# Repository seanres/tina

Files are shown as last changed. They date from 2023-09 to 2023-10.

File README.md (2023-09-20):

# tira
Robot arm project for UConn's robotics club!

WIP page

## To Do:

- [ ] Order materials

Mechanical
- [ ] Design review
- [ ] 3D printing process
- [ ] Print arm components
- [ ] Overall solidoworks part design
- [ ] Assembly in solidworks
- [ ] Modifying design for gears
- [ ] Blueprints?
- [ ] Machining process
- [ ] Machining aluminum parts

Electrical
- [ ] Electrical design review
- [ ] Review basic electronics (laser video)
- [ ] Soldering/wiring overview
- [ ] Review microcontrollers/arduinos
- [ ] Basic motor control 
- [ ] Assemble circuitry

Digital
- [ ] Programming for arudino
- [ ] ROS introduction
- [ ] ROS for robot arm
- [ ] More advanced ROS control
- [ ] Control theory? (PID)
- [ ] Communication? (I2C, serial)

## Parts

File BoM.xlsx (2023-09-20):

Notes | Name | Link | # Reqd. | # per Unit | Unit Cost | # To Order | Total
 | Motors:
 | Nema 8 (8HS13-0604S) 33mm | https://www.oyostepper.com/goods-3-Nema-8-Stepper-Motor-Bipolar-18-deg-2Ncm-283ozin-06A-39V-20x20x33mm-4-Wires.html | 1 | 1 | $22.36 | 1 | $22.36
 | Nema 11 (11HS12-0674S) 31mm | https://www.omc-stepperonline.com/nema-11-bipolar-1-8deg-7ncm-9-91oz-in-0-67a-3-8v-28x28x31mm-4-wires-11hs12-0674s | 2 | 1 | $10.18 | 2 | $20.36
 | Nema 17 (17HS19-0854S) 48mm | https://www.omc-stepperonline.com/nema-17-bipolar-1-8deg-44ncm-62-3oz-in-0-85a-5-3v-42x42x48mm-4-wires-17hs19-0854s | 1 | 1 | $10.85 | 1 | $10.85
 | Nema 23 (23HS30-2804S1) 76mm | https://www.omc-stepperonline.com/nema-23-bipolar-1-9nm-269oz-in-2-8a-57x57x76mm-4wires-6mm-shaft-23hs30-2804s1 | 2 | 1 | $29.85 | 2 | $59.70
https://shop.sdp-si.com/catalog/?cid=p342&sort=undefined&view=table | Belts: |  |  |  |  |  | $0.00
 | A 6R51M087060, 87 teeth GT2 2mm, 6mm wide timing belt | https://shop.sdp-si.com/catalog/product/?id=A_6R51M087060 | 2 | 1 | $6.71 | 2 | $13.42
 | A 6R51M139060, 139 teeth GT2 2mm, 6mm wide timing belt | https://shop.sdp-si.com/catalog/product/?id=A_6R51M139060 | 1 | 1 | $7.67 | 1 | $7.67
OOS, 2mm pitch instead | A 6R53M128090, 128 teeth GT2 3mm, 9mm wide timing belt | https://shop.sdp-si.com/catalog/product/?id=A_6R51M128090 | 1 | 1 | $10.14 | 1 | $10.14
OOS, 2mm pitch instead | A 6R53M152090, 152 teeth GT2 3mm, 9mm wide timing belt | https://shop.sdp-si.com/catalog/product/?id=A36R51M152090 | 1 | 1 | $8.09 | 1 | $8.09
https://shop.sdp-si.com/catalog/?cid=p346 | Pulleys: |  |  |  |  |  | $0.00
 | GT2 Pulley (20 Tooth), GT2 2mm, 20 teeth, 5mm bore | https://quantum3dprinting.com/shop/genuine-e3d-2gt-pulley-20-tooth-m-2gt-pulley-20t/ | 3 | 1 | $10.98 | 3 | $32.94
 | A 6A53M020DF0906, GT2 3mm, 20 teeth, 6mm bore | https://shop.sdp-si.com/catalog/product/?id=A_6A53M020DF0906 | 2 | 1 | $10.88 | 2 | $21.76
 | Bearings: |  |  |  |  |  | $0.00
DISCONTINUED, NEED ALTERNATIVE | Ball Bearing, 21x15x4mm |  | 3 | 4 | $8.59 | 1 | $8.59
 | Ball Bearing, 16x8x5mm | https://www.amazon.com/Hobbypower-8x16x5mm-Shielded-16x8x5mm-Bearings/dp/B07WVJWQZS | 3 | 10 | $7.99 | 1 | $7.99
DISCONTINUED, NEED ALTERNATIVE | Ball Bearing, 8x3x3mm |  | 4 | 1 | $2.00 | 4 | $8.00
 | Q6000 ZZ, 26x10x8mm | https://www.amazon.com/FKG-6000-ZZ-10x26x8mm-Bearing-Pre-Lubricated/dp/B07T59CWXX | 2 | 19 | $9.97 | 1 | $9.97
 | Q625 ZZ, 16x5x5mm | https://www.ebay.com/itm/333771184305 | 4 | 6 | $7.68 | 1 | $7.68
 | Q6001 ZZ, 28x12x8mm | https://www.amazon.com/PGN-6001-ZZ-Shielded-Ball-Bearing/dp/B07GVQ6K9R?s=industrial | 2 | 10 | $10.90 | 1 | $10.90
European, need to find US source | TB51102, 28x16x28x15x9mm | https://www.amazon.com/51102-Thrust-Bearing-15x28x9-Bearings/dp/B002BBKMZO | 2 | 1 | $10.00 | 2 | $20.00
 | Carbon Fiber:
 | Axis3part1 (3mm thickness) |  | 2 |  |  |  | $200.00
 | Axis2part1 (4mm thickness) |  | 2
 | Axis1part2 (4mm thickness) |  | 2
 | Screws and Nuts:
 | M2x6mm |  | 1
 | M2x8mm + nut |  | 4
 | M2x12mm + nut |  | 3
 | M2x10mm + nut |  | 1
 | M2.5x8mm + washer |  | 8
 | M3x10mm + nut + washer |  | 1
 | M3x12mm + nut + washer |  | 14
 | M3x16mm + nut + washer |  | 2
 | M3x20mm + nut + washer |  | 6
 | M3x25mm + washer |  | 4
 | M3x25mm + nut |  | 1
 | M3x30mm + nut + washer |  | 6
 | M3 washer |  | 10
 | M4x12mm + nut + washer |  | 8
 | M5x10mm + washer |  | 12
 | M5x20mm + washer |  | 2
 | M5x35mm + nut + washer |  | 4
 | M5x40mm + nut + washer |  | 1
 | M5x50mm + nut + washer |  | 16
 | M5 washer |  | 10
 | M5 threaded standoff, 8mm OD, 20mm Len |  | 7
 |  | https://www.amazon.com/VIGRUE-M2-M3-M4-1080PCS-Stainless-Screws-Socket/dp/B071KBVZVV?s=industrial | 1 |  | estimate: | 2 | 50
 | Other Parts:
 | Magnet 6mm diameter, 2mm height
 | DP2.0-6/B, dowel pin 2x6
 | Tube: 8mm OD, 6mm, ID, 70mm Len
 | Tube: 10mm OD, 8mm ID, 115m len
 | Tube: 12mm OD, 10mm ID, 106mm len
 | Silicon insulated high quality wires
 | Rubber feed with M3 set
 |  |  |  |  |  |  | 60
 | Controllers:
KIT #1 | A4988 Stepper Motor Driver Module | https://www.amazon.com/Stepper-Printer-StepStick-Envistia-Mall/dp/B07QT7N3T2 | 3 | 2 | $5.89 | 0
 | TB6600 4A 9-42V stepper motor driver | https://www.amazon.com/TB6600-Stepper-Driver-Controller-tb6600/dp/B07RRB6BGQ | 3 | 4 | $33.99 | 1
 | Microcontroller:
KIT #1 | 3D printer RAMPS control board | https://www.amazon.com/Controller-MEGA2560-Soldered-Stepper-Drivers/dp/B08N578PRN | 1 | 1 | $31.39 | 1
KIT #1 | Arduino Mega 2560 |  | 1
 | Connectors:
 | D-sub 25, male connector |  | 1 |  |  |  | 5
 | D-sub 25, female connector |  | 1 |  |  |  | 5
 | Wires:
 | D-sub 25 male - D-sub 25 female, 3.0Amp rating |  | 1 |  |  |  | 10
 | Miscillaneous:
 | Soddering Iron Kit | https://www.amazon.com/gp/product/B00ANZRT4M/ref=ppx_yo_dt_b_search_asin_title?ie=UTF8&psc=1 | 1 |  | $75.99 |  | 115
 | Soddering Iron Wire Holder |  | 1
 |  |  |  |  |  | SUM: | $725.42

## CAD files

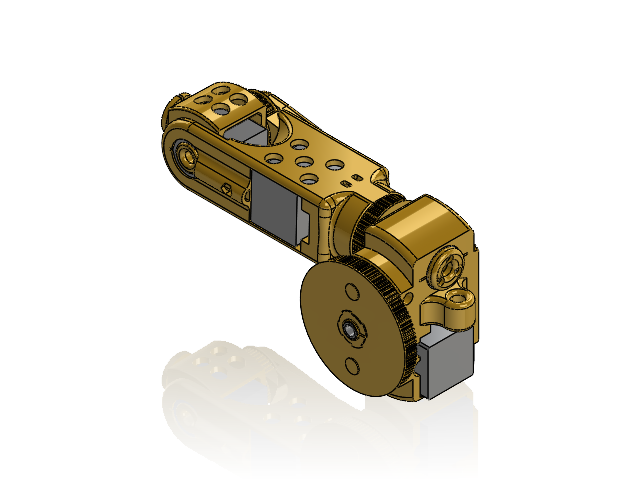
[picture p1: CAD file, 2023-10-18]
SolidWorks/upper_assembly.SLDASM
Bearing21_15_4_3 x 3
Pulley42
Bearing16_8_5_1_1
Nema8_1
Axis6_1
axis6motorHolder_1
Pulley100
Pulley56
Nema11_2 x 2
Axis5
Axis4
Axis5Bracket
Axis4limit
Axis5plug
Axis5screwHolder
Axis3tube

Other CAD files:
SolidWorks/Bearing16_8_5_3.SLDASM
SolidWorks/Bearing16_8_5.SLDASM
SolidWorks/Axis2part1_1.SLDASM
SolidWorks/Bearing26_10_8.SLDASM
SolidWorks/Axis3part1_1.SLDASM
SolidWorks/Nema11.SLDASM
SolidWorks/Axis5Pulley.SLDASM
SolidWorks/Axis1Pulley.SLDASM
SolidWorks/Bearing28_12_8_1.SLDASM
SolidWorks/Bearing21_15_4.SLDASM
SolidWorks/Nema17.SLDASM
SolidWorks/Axis3part1.SLDASM
SolidWorks/Axis1part2.SLDASM
SolidWorks/Axis6.SLDASM
SolidWorks/Axis3Pulley.SLDASM
SolidWorks/axis6motorHolder.SLDASM
SolidWorks/ThrustBearing28_15_9_1.SLDASM
Axis/Axis1tube.f3d
Axis/Axis1tube.step
Axis/Axis2tube.f3d
Axis/Axis2tube.step
Axis/Axis3tube.f3d
Axis/Axis3tube.step
CarbonFibre/Axis1part2.DXF
CarbonFibre/Axis1part2.stl
CarbonFibre/Axis2part1.DXF
CarbonFibre/Axis2part1.stl
CarbonFibre/Axis3part1.DXF
CarbonFibre/Axis3part1.stl
Fusion360/Axis6 v13.step
Fusion360/AxisTot1 v14.step
Fusion360/AxisTot1.f3z
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

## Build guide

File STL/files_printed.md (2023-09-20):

Axis1Holder.stl - x1 unit
Axis1MotorHolder.stl - x1 unit
Axis1MotorHolderOp.stl - x1 unit
Axis1part2.stl - x2 units (optional, only if you do not have carbon fibre parts)
Axis1Pulley.stl - x1 unit
Axis1washer.stl - x1 unit
Axis2bearingHC.stl - x1 unit
Axis2bearingHolder (1).stl - x1 unit
Axis2bearingHolder.stl - x1 unit
Axis2MotorOp.stl - x1 unit
Axis2MotorOpC.stl - x1 unit
Axis2part1.stl - x2 units (optional, only if you do not have carbon fibre parts)
Axis2part2.stl - x1 unit
Axis2Pulley.stl - x1 unit
Axis2washer.stl - x1 unit
Axis3bearingHolder.stl - x2 units
Axis3cover1.stl - x1 unit
Axis3cover2.stl - x1 unit
Axis3part1.stl - x2 units (optional, only if you do not have carbon fibre parts)
Axis3part2.stl - x1 unit
Axis3part3.stl - x1 unit
Axis4.stl - x1 unit
Axis4limit.stl - x1 unit
- [X] Axis5.stl - x1 unit
- [X] Axis5Bracket.stl - x1 unit
- [X] Axis5plug.stl - x1 unit
- [X] Axis5screwHolder.stl - x1 unit
- [X] Axis6.stl - x1 unit
- [X] axis6motorHolder.stl - x1 unit
FootHolder.stl - x2 units
LegLeft.stl - x1 unit and x1 unit mirrored part
Pulley42.stl - x1 unit
Pulley56.stl - x1 unit
Pulley100.stl - x1 unit
Electronics.stl - support for the Arduino and TB6600 drivers for electronics

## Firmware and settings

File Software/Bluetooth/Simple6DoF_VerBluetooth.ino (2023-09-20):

/*
Simple script to move my tiny 6dof robotic arm
*/
#include <math.h>
//#include <SoftwareSerial.h>

#define PI 3.1415926535897932384626433832795

//driver for the axis 1
#define PUL1_PIN 39
#define DIR1_PIN 37
//driver for the axis 2
#define PUL2_PIN 43
#define DIR2_PIN 41
//driver for the axis 3
#define PUL3_PIN 47
#define DIR3_PIN 45
//driver for the axis 4
#define PUL4_PIN 46
#define DIR4_PIN 48
//driver for the axis 5
#define PUL5_PIN A6
#define DIR5_PIN A7
//driver for the axis 6
#define PUL6_PIN A0
#define DIR6_PIN A1

//enable pin for the axis 3, 2 and 1
#define EN321_PIN 32
#define EN4_PIN A8
#define EN5_PIN A2
#define EN6_PIN 38

double curPos1 = 0.0;
double curPos2 = -78.51;
double curPos3 = 73.90;
double curPos4 = 0.0;
double curPos5 = -90.0;
double curPos6 = 0.0;

boolean PULstat1 = 0;
boolean PULstat2 = 0;
boolean PULstat3 = 0;
boolean PULstat4 = 0;
boolean PULstat5 = 0;
boolean PULstat6 = 0;

//robot geometry
const double dl1 = 360.0/200.0/32.0/4.8;
const double dl2 = 360.0/200.0/32.0/4.0;
const double dl3 = 360.0/200.0/32.0/5.0;
const double dl4 = 360.0/200.0/32.0/2.8;
const double dl5 = 360.0/200.0/32.0/2.1;
const double dl6 = 360.0/200.0/32.0/1.0;
const double r1 = 47.0;
const double r2 = 110.0;
const double r3 = 26.0; 
const double d1 = 133.0;
const double d3 = 0.0;
const double d4 = 117.50;
const double d6 = 28.0;

//SoftwareSerial Bluetooth(29, 31); // Arduino(RX, TX) - HC-05 Bluetooth (TX, RX)
String dataIn = ""; //variable to store the bluetooth command
double futPos1 = 0.0;
double futPos2 = 0.0;
double futPos3 = 0.0;
double futPos4 = 0.0;
double futPos5 = 0.0;
double futPos6 = 0.0;
double curSpeed = 0.3*0.5e-4;
double curFinalSpeed = 0.0;
int index = 0; //index corresonding to the robot position
float Joint1[50], Joint2[50], Joint3[50], Joint4[50], Joint5[50], Joint6[50], MaxSpeed[50], InSpeed[50], FinSpeed[50];

void setup()
{
  //Bluetooth.begin(38400); // Default baud rate of the Bluetooth module
  //Bluetooth.setTimeout(1);
  Serial1.begin(9600);
  //Serial1.setTimeout(3);
  delay(20);

  pinMode(PUL1_PIN, OUTPUT);
  pinMode(DIR1_PIN, OUTPUT);
  pinMode(PUL2_PIN, OUTPUT);
  pinMode(DIR2_PIN, OUTPUT);
  pinMode(PUL3_PIN, OUTPUT);
  pinMode(DIR3_PIN, OUTPUT);
  pinMode(PUL4_PIN, OUTPUT);
  pinMode(DIR4_PIN, OUTPUT);
  pinMode(PUL5_PIN, OUTPUT);
  pinMode(DIR5_PIN, OUTPUT);
  pinMode(PUL6_PIN, OUTPUT);
  pinMode(DIR6_PIN, OUTPUT);

  pinMode(EN321_PIN, OUTPUT);
  pinMode(EN4_PIN, OUTPUT);
  pinMode(EN5_PIN, OUTPUT);
  pinMode(EN6_PIN, OUTPUT);
  
  digitalWrite(PUL1_PIN, LOW); // gear ratio = 96/20 = 4.8
  digitalWrite(DIR1_PIN, LOW); //LOW = negative direction
  
  digitalWrite(PUL2_PIN, LOW); // gear ratio = 4
  digitalWrite(DIR2_PIN, LOW); //LOW = positive direction
  
  digitalWrite(PUL3_PIN, LOW); // gear ratio = 5
  digitalWrite(DIR3_PIN, LOW); //LOW = negative direction
  
  digitalWrite(PUL4_PIN, LOW); // gear ratio = 56/20 = 2.8
  digitalWrite(DIR4_PIN, LOW); //LOW = positive direction
  
  digitalWrite(PUL5_PIN, LOW); // gear ratio = 42/20 = 2.1
  digitalWrite(DIR5_PIN, LOW); //LOW = positive direction
  
  digitalWrite(PUL6_PIN, LOW); // gear ratio = 1
  digitalWrite(DIR6_PIN, LOW); //LOW = positive direction

  // all joints disabled!
  digitalWrite(EN321_PIN, HIGH);
  digitalWrite(EN4_PIN, HIGH);
  digitalWrite(EN5_PIN, HIGH);
  digitalWrite(EN6_PIN, HIGH); 

  //Serial.begin(9600);
}

void loop()
{
  //Serial1.write("Hello");
  // Check for incoming data
  if (Serial1.available() > 0) {
    dataIn = Serial1.readString();  // Read the data as string

    //Serial.println(dataIn);
    if (dataIn == "enable") {
      digitalWrite(EN321_PIN, LOW);
      digitalWrite(EN4_PIN, LOW);
      digitalWrite(EN5_PIN, LOW);
      digitalWrite(EN6_PIN, LOW);
    }
    
    if (dataIn == "disable") {
      digitalWrite(EN321_PIN, HIGH);
      digitalWrite(EN4_PIN, HIGH);
      digitalWrite(EN5_PIN, HIGH);
      digitalWrite(EN6_PIN, HIGH);
    }

    if (dataIn.startsWith("s6")) {
      String dataInS = dataIn.substring(2, dataIn.length());
      futPos6 = dataInS.toFloat();
      float Jinitial[6]={curPos1, curPos2, curPos3, curPos4, curPos5, curPos6};
      float Jfinal[6]={curPos1, curPos2, curPos3, curPos4, curPos5, futPos6};
      goStrightLine(Jinitial, Jfinal, curSpeed, 0.75e-10, 0.0, 0.0);
    }

    if (dataIn.startsWith("s5")) {
      String dataInS = dataIn.substring(2, dataIn.length());
      futPos5 = dataInS.toFloat();
      float Jinitial[6]={curPos1, curPos2, curPos3, curPos4, curPos5, curPos6};
      float Jfinal[6]={curPos1, curPos2, curPos3, curPos4, futPos5, curPos6};
      goStrightLine(Jinitial, Jfinal, curSpeed, 0.75e-10, 0.0, 0.0);
    }

    if (dataIn.startsWith("s4")) {
      String dataInS = dataIn.substring(2, dataIn.length());
      futPos4 = dataInS.toFloat();
      float Jinitial[6]={curPos1, curPos2, curPos3, curPos4, curPos5, curPos6};
      float Jfinal[6]={curPos1, curPos2, curPos3, futPos4, curPos5, curPos6};
      goStrightLine(Jinitial, Jfinal, curSpeed, 0.75e-10, 0.0, 0.0);
    }

    if (dataIn.startsWith("s3")) {
      String dataInS = dataIn.substring(2, dataIn.length());
      futPos3 = dataInS.toFloat();
      float Jinitial[6]={curPos1, curPos2, curPos3, curPos4, curPos5, curPos6};
      float Jfinal[6]={curPos1, curPos2, futPos3, curPos4, curPos5, curPos6};
      goStrightLine(Jinitial, Jfinal, curSpeed, 0.75e-10, 0.0, 0.0);
    }

    if (dataIn.startsWith("s2")) {
      String dataInS = dataIn.substring(2, dataIn.length());
      futPos2 = dataInS.toFloat();
      float Jinitial[6]={curPos1, curPos2, curPos3, curPos4, curPos5, curPos6};
      float Jfinal[6]={curPos1, futPos2, curPos3, curPos4, curPos5, curPos6};
      goStrightLine(Jinitial, Jfinal, curSpeed, 0.75e-10, 0.0, 0.0);
    }
    
    if (dataIn.startsWith("s1")) {
      String dataInS = dataIn.substring(2, dataIn.length());
      futPos1 = dataInS.toFloat();
      float Jinitial[6]={curPos1, curPos2, curPos3, curPos4, curPos5, curPos6};
      float Jfinal[6]={futPos1, curPos2, curPos3, curPos4, curPos5, curPos6};
      goStrightLine(Jinitial, Jfinal, curSpeed, 0.75e-10, 0.0, 0.0);
    }

    // set the maximum speed for the move
    if (dataIn.startsWith("ss")) {
      String dataInS = dataIn.substring(2, dataIn.length());
      curSpeed = (dataInS.toFloat()/100)*0.5e-4;
    }

    // If button "SAVE" is pressed
    if (dataIn.startsWith("save")) {
      String dataInS = dataIn.substring(4, dataIn.length());
      InSpeed[index] = curFinalSpeed;
      curFinalSpeed = (dataInS.toFloat()/100)*0.5e-4;
      Joint1[index] = curPos1;  // save position into the array
      Joint2[index] = curPos2;
      Joint3[index] = curPos3;
      Joint4[index] = curPos4;
      Joint5[index] = curPos5;
      Joint6[index] = curPos6;
      MaxSpeed[index] = curSpeed;
      FinSpeed[index] = curFinalSpeed;
      index++;                        // Increase the array index
    }

    if ( dataIn == "reset") {
      index = 0;  // Index to 0
    }

    if (dataIn.startsWith("run")) {
      float Jinitial[6]={curPos1, curPos2, curPos3, curPos4, curPos5, curPos6};
      float Jfinal[6]={Joint1[0], Joint2[0], Joint3[0], Joint4[0], Joint5[0], Joint6[0]};
      goStrightLine(Jinitial, Jfinal, MaxSpeed[0], 0.75e-10, 0.0, 0.0);
      for (int i = 0; i <= index - 2; i++) {  // Run through all steps(index)
        float Jinitial[6]={Joint1[i], Joint2[i], Joint3[i], Joint4[i], Joint5[i], Joint6[i]};
        float Jfinal[6]={Joint1[i+1], Joint2[i+1], Joint3[i+1], Joint4[i+1], Joint5[i+1], Joint6[i+1]};
        goStrightLine(Jinitial, Jfinal, MaxSpeed[i+1], 0.75e-10, InSpeed[i+1], FinSpeed[i+1]);
      }
    }

  }
}


void goStrightLine(float* xfi, float* xff, float vel0, float acc0, float velini, float velfin){
  //
  float lmax = max(abs(xff[0]-xfi[0]),abs(xff[1]-xfi[1]));
  lmax = max(lmax,abs(xff[2]-xfi[2]));
  lmax = max(lmax,abs(xff[3]-xfi[3]));
  lmax = max(lmax,abs(xff[4]-xfi[4]));
  lmax = max(lmax,abs(xff[5]-xfi[5]));
  unsigned long preMil = micros();
  double l = 0.0;
  vel0 = min(vel0,sqrt(lmax*acc0+0.5*velini*velini+0.5*velfin*velfin));
  unsigned long curMil = micros();
  unsigned long t = 0;
  double tap = vel0/acc0-velini/acc0;
  double lap = velini*tap+acc0*tap*tap/2.0;
  double lcsp = lmax-(vel0*vel0/2.0/acc0-velfin*velfin/2.0/acc0);
  double tcsp = (lcsp-lap)/vel0+tap;
  double tfin = vel0/acc0-velfin/acc0+tcsp;
  while (curMil-preMil<=tfin){
    t = curMil-preMil;
    //acceleration phase
    if (t<=tap) {
      l = velini*t+acc0*t*t/2.0;
    }
    //contant maximum speed phase
    if (t>tap && t<=tcsp) {
      l = lap+vel0*(t-tap);
    }
    //deceleration phase
    if (t>tcsp) {
      l = lcsp+vel0*(t-tcsp)-acc0*(t-tcsp)*(t-tcsp)/2.0;
    }
  
    //trajectory x and y as a function of l
    float Xx[6];
    Xx[0]=xfi[0]+(xff[0]-xfi[0])/lmax*l;
    Xx[1]=xfi[1]+(xff[1]-xfi[1])/lmax*l;
    Xx[2]=xfi[2]+(xff[2]-xfi[2])/lmax*l;
    Xx[3]=xfi[3]+(xff[3]-xfi[3])/lmax*l;
    Xx[4]=xfi[4]+(xff[4]-xfi[4])/lmax*l;
    Xx[5]=xfi[5]+(xff[5]-xfi[5])/lmax*l;
    
    goTrajectory(Xx);
    curMil = micros();
  }
}

void goTrajectory(float* Jf){
  
  //execution
  int delF=2;
  // joint #1
  if (Jf[0]-curPos1>0.0) { // positive direction of rotation
    digitalWrite(DIR1_PIN, HIGH);
    while (Jf[0]-curPos1>dl1/2.0) {
      if (PULstat1 == 0) {
        digitalWrite(PUL1_PIN, HIGH);
        PULstat1 = 1;
      } else {
        digitalWrite(PUL1_PIN, LOW);
        PULstat1 = 0;
      }
      //curPos1 = Jf[0];
      curPos1 = curPos1 + dl1/2.0;
      if (Jf[0]-curPos1>dl1/2.0) {
        delayMicroseconds(delF);
      }
    }
  } else {
    digitalWrite(DIR1_PIN, LOW);
    while (-Jf[0]+curPos1>dl1/2.0) {
      if (PULstat1 == 0) {
        digitalWrite(PUL1_PIN, HIGH);
        PULstat1 = 1;
      } else {
        digitalWrite(PUL1_PIN, LOW);
        PULstat1 = 0;
      }
      //curPos1 = Jf[0];
      curPos1 = curPos1 - dl1/2.0;
      if (-Jf[0]+curPos1>dl1/2.0) {
        delayMicroseconds(delF);
      }
    }
  }
  // joint #2
  if (Jf[1]-curPos2>0.0) { // positive direction of rotation
    digitalWrite(DIR2_PIN, HIGH);
    while (Jf[1]-curPos2>dl2/2.0) {
      if (PULstat2 == 0) {
        digitalWrite(PUL2_PIN, HIGH);
        PULstat2 = 1;
      } else {
        digitalWrite(PUL2_PIN, LOW);
        PULstat2 = 0;
      }
      //curPos2 = Jf[1];
      curPos2 = curPos2 + dl2/2.0;
      if (Jf[1]-curPos2>dl2/2.0) {
        delayMicroseconds(delF);
      }
    }
  } else {
    digitalWrite(DIR2_PIN, LOW);
    while (-Jf[1]+curPos2>dl2/2.0) {
      if (PULstat2 == 0) {
        digitalWrite(PUL2_PIN, HIGH);
        PULstat2 = 1;
      } else {
        digitalWrite(PUL2_PIN, LOW);
        PULstat2 = 0;
      }
      //curPos2 = Jf[1];
      curPos2 = curPos2 - dl2/2.0;
      if (-Jf[1]+curPos2>dl2/2.0) {
        delayMicroseconds(delF);
      }
    }
  }
  // joint #3
  if (Jf[2]-curPos3>0.0) { // positive direction of rotation
    digitalWrite(DIR3_PIN, LOW);
    while (Jf[2]-curPos3>dl3/2.0) {
      if (PULstat3 == 0) {
        digitalWrite(PUL3_PIN, HIGH);
        PULstat3 = 1;
      } else {
        digitalWrite(PUL3_PIN, LOW);
        PULstat3 = 0;
      }
      //curPos3 = Jf[2];
      curPos3 = curPos3 + dl3/2.0;
      if (Jf[2]-curPos3>dl3/2.0) {
        delayMicroseconds(delF);
      }
    }
  } else {
    digitalWrite(DIR3_PIN, HIGH);
    while (-Jf[2]+curPos3>dl3/2.0) {
      if (PULstat3 == 0) {
        digitalWrite(PUL3_PIN, HIGH);
        PULstat3 = 1;
      } else {
        digitalWrite(PUL3_PIN, LOW);
        PULstat3 = 0;
      }
      //curPos3 = Jf[2];
      curPos3 = curPos3 - dl3/2.0;
      if (-Jf[2]+curPos3>dl3/2.0) {
        delayMicroseconds(delF);
      }
    }
  }
  // joint #4
  if (Jf[3]-curPos4>0.0) { // positive direction of rotation
    digitalWrite(DIR4_PIN, HIGH);
    while (Jf[3]-curPos4>dl4/2.0) {
      if (PULstat4 == 0) {
        digitalWrite(PUL4_PIN, HIGH);
        PULstat4 = 1;
      } else {
        digitalWrite(PUL4_PIN, LOW);
        PULstat4 = 0;
      }
      //curPos4 = Jf[3];
      curPos4 = curPos4 + dl4/2.0;
      if (Jf[3]-curPos4>dl4/2.0) {
        delayMicroseconds(delF);
      }
    }
  } else {
    digitalWrite(DIR4_PIN, LOW);
    while (-Jf[3]+curPos4>dl4/2.0) {
      if (PULstat4 == 0) {
        digitalWrite(PUL4_PIN, HIGH);
        PULstat4 = 1;
      } else {
        digitalWrite(PUL4_PIN, LOW);
        PULstat4 = 0;
      }
      //curPos4 = Jf[3];
      curPos4 = curPos4 - dl4/2.0;
      if (-Jf[3]+curPos4>dl4/2.0) {
        delayMicroseconds(delF);
      }
    }
  }
  // joint #5
  if (Jf[4]-curPos5>0.0) { // positive direction of rotation
    digitalWrite(DIR5_PIN, HIGH);
    while (Jf[4]-curPos5>dl5/2.0) {
      if (PULstat5 == 0) {
        digitalWrite(PUL5_PIN, HIGH);
        PULstat5 = 1;
      } else {
        digitalWrite(PUL5_PIN, LOW);
        PULstat5 = 0;
      }
      //curPos5 = Jf[4];
      curPos5 = curPos5 + dl5/2.0;
      if (Jf[4]-curPos5>dl5/2.0) {
        delayMicroseconds(delF);
      }
    }
  } else {
    digitalWrite(DIR5_PIN, LOW);
    while (-Jf[4]+curPos5>dl5/2.0) {
      if (PULstat5 == 0) {
        digitalWrite(PUL5_PIN, HIGH);
        PULstat5 = 1;
      } else {
        digitalWrite(PUL5_PIN, LOW);
        PULstat5 = 0;
      }
      //curPos5 = Jf[4];
      curPos5 = curPos5 - dl5/2.0;
      if (-Jf[4]+curPos5>dl5/2.0) {
        delayMicroseconds(delF);
      }
    }
  }
  // joint #6
  if (Jf[5]-curPos6>0.0) { // positive direction of rotation
    digitalWrite(DIR6_PIN, HIGH);
    while (Jf[5]-curPos6>dl6/2.0) {
      if (PULstat6 == 0) {
        digitalWrite(PUL6_PIN, HIGH);
        PULstat6 = 1;
      } else {
        digitalWrite(PUL6_PIN, LOW);
        PULstat6 = 0;
      }
      //curPos6 = Jf[5];
      curPos6 = curPos6 + dl6/2.0;
      if (Jf[5]-curPos6>dl6/2.0) {
        delayMicroseconds(delF);
      }
    }
  } else {
    digitalWrite(DIR6_PIN, LOW);
    while (-Jf[5]+curPos6>dl6/2.0) {
      if (PULstat6 == 0) {
        digitalWrite(PUL6_PIN, HIGH);
        PULstat6 = 1;
      } else {
        digitalWrite(PUL6_PIN, LOW);
        PULstat6 = 0;
      }
      //curPos6 = Jf[5];
      curPos6 = curPos6 - dl6/2.0;
      if (-Jf[5]+curPos6>dl6/2.0) {
        delayMicroseconds(delF);
      }
    }
  }
}

void InverseK(float* Xik, float* Jik)
{
  // inverse kinematics
  // input: Xik - pos value for the calculation of the inverse kinematics
  // output: Jfk - joints value for the calculation of the inversed kinematics
  
  // from deg to rad
  // Xik(4:6)=Xik(4:6)*pi/180;
  Xik[3]=Xik[3]*PI/180.0;
  Xik[4]=Xik[4]*PI/180.0;
  Xik[5]=Xik[5]*PI/180.0;
  
  // Denavit-Hartenberg matrix
  float theta[6]={0.0, -90.0, 0.0, 0.0, 0.0, 0.0}; // theta=[0; -90+0; 0; 0; 0; 0];
  float alfa[6]={-90.0, 0.0, -90.0, 90.0, -90.0, 0.0}; // alfa=[-90; 0; -90; 90; -90; 0];
  float r[6]={r1, r2, r3, 0.0, 0.0, 0.0}; // r=[47; 110; 26; 0; 0; 0];
  float d[6]={d1, 0.0, d3, d4, 0.0, d6}; // d=[133; 0; 7; 117.5; 0; 28];
  // from deg to rad
  MatrixScale(theta, 6, 1, PI/180.0); // theta=theta*pi/180;
  MatrixScale(alfa, 6, 1, PI/180.0); // alfa=alfa*pi/180;
  
  // work frame
  float Xwf[6]={0.0, 0.0, 0.0, 0.0, 0.0, 0.0}; // Xwf=[0; 0; 0; 0; 0; 0];
  
  // tool frame
  float Xtf[6]={0.0, 0.0, 0.0, 0.0, 0.0, 0.0}; // Xtf=[0; 0; 0; 0; 0; 0];
  
  // work frame transformation matrix
  float Twf[16];
  pos2tran(Xwf, Twf); // Twf=pos2tran(Xwf);
  
  // tool frame transformation matrix
  float Ttf[16];
  pos2tran(Xtf, Ttf); // Ttf=pos2tran(Xtf);
  
  // total transformation matrix
  float Twt[16];
  pos2tran(Xik, Twt); // Twt=pos2tran(Xik);
  
  // find T06
  float inTwf[16], inTtf[16], Tw6[16], T06[16];
  invtran(Twf, inTwf); // inTwf=invtran(Twf);
  invtran(Ttf, inTtf); // inTtf=invtran(Ttf);
  MatrixMultiply(Twt, inTtf, 4, 4, 4, Tw6); // Tw6=Twt*inTtf;
  MatrixMultiply(inTwf, Tw6, 4, 4, 4, T06); // T06=inTwf*Tw6;
  
  // positon of the spherical wrist
  float Xsw[3];
  // Xsw=T06(1:3,4)-d(6)*T06(1:3,3);
  Xsw[0]=T06[0*4 + 3]-d[5]*T06[0*4 + 2];
  Xsw[1]=T06[1*4 + 3]-d[5]*T06[1*4 + 2];
  Xsw[2]=T06[2*4 + 3]-d[5]*T06[2*4 + 2];
  
  // joints variable
  // Jik=zeros(6,1);
  // first joint
  Jik[0]=atan2(Xsw[1],Xsw[0])-atan2(d[2],sqrt(Xsw[0]*Xsw[0]+Xsw[1]*Xsw[1]-d[2]*d[2])); // Jik(1)=atan2(Xsw(2),Xsw(1))-atan2(d(3),sqrt(Xsw(1)^2+Xsw(2)^2-d(3)^2));
  // second joint
  Jik[1]=PI/2.0
  -acos((r[1]*r[1]+(Xsw[2]-d[0])*(Xsw[2]-d[0])+(sqrt(Xsw[0]*Xsw[0]+Xsw[1]*Xsw[1]-d[2]*d[2])-r[0])*(sqrt(Xsw[0]*Xsw[0]+Xsw[1]*Xsw[1]-d[2]*d[2])-r[0])-(r[2]*r[2]+d[3]*d[3]))/(2.0*r[1]*sqrt((Xsw[2]-d[0])*(Xsw[2]-d[0])+(sqrt(Xsw[0]*Xsw[0]+Xsw[1]*Xsw[1]-d[2]*d[2])-r[0])*(sqrt(Xsw[0]*Xsw[0]+Xsw[1]*Xsw[1]-d[2]*d[2])-r[0]))))
  -atan((Xsw[2]-d[0])/(sqrt(Xsw[0]*Xsw[0]+Xsw[1]*Xsw[1]-d[2]*d[2])-r[0])); // Jik(2)=pi/2-acos((r(2)^2+(Xsw(3)-d(1))^2+(sqrt(Xsw(1)^2+Xsw(2)^2-d(3)^2)-r(1))^2-(r(3)^2+d(4)^2))/(2*r(2)*sqrt((Xsw(3)-d(1))^2+(sqrt(Xsw(1)^2+Xsw(2)^2-d(3)^2)-r(1))^2)))-atan((Xsw(3)-d(1))/(sqrt(Xsw(1)^2+Xsw(2)^2-d(3)^2)-r(1)));
  // third joint
  Jik[2]=PI
  -acos((r[1]*r[1]+r[2]*r[2]+d[3]*d[3]-(Xsw[2]-d[0])*(Xsw[2]-d[0])-(sqrt(Xsw[0]*Xsw[0]+Xsw[1]*Xsw[1]-d[2]*d[2])-r[0])*(sqrt(Xsw[0]*Xsw[0]+Xsw[1]*Xsw[1]-d[2]*d[2])-r[0]))/(2*r[1]*sqrt(r[2]*r[2]+d[3]*d[3])))
  -atan(d[3]/r[2]); // Jik(3)=pi-acos((r(2)^2+r(3)^2+d(4)^2-(Xsw(3)-d(1))^2-(sqrt(Xsw(1)^2+Xsw(2)^2-d(3)^2)-r(1))^2)/(2*r(2)*sqrt(r(3)^2+d(4)^2)))-atan(d(4)/r(3));
  // last three joints
  float T01[16], T12[16], T23[16], T02[16], T03[16], inT03[16], T36[16];
  DH1line(theta[0]+Jik[0], alfa[0], r[0], d[0], T01); // T01=DH1line(theta(1)+Jik(1),alfa(1),r(1),d(1));
  DH1line(theta[1]+Jik[1], alfa[1], r[1], d[1], T12); // T12=DH1line(theta(2)+Jik(2),alfa(2),r(2),d(2));
  DH1line(theta[2]+Jik[2], alfa[2], r[2], d[2], T23); // T23=DH1line(theta(3)+Jik(3),alfa(3),r(3),d(3));
  MatrixMultiply(T01, T12, 4, 4, 4, T02); // T02=T01*T12;
  MatrixMultiply(T02, T23, 4, 4, 4, T03); // T03=T02*T23;
  invtran(T03, inT03); // inT03=invtran(T03);
  MatrixMultiply(inT03, T06, 4, 4, 4, T36); // T36=inT03*T06;
  // forth joint
  Jik[3]=atan2(-T36[1*4+2], -T36[0*4+2]); // Jik(4)=atan2(-T36(2,3),-T36(1,3));
  // fifth joint
  Jik[4]=atan2(sqrt(T36[0*4+2]*T36[0*4+2]+T36[1*4+2]*T36[1*4+2]), T36[2*4+2]); // Jik(5)=atan2(sqrt(T36(1,3)^2+T36(2,3)^2),T36(3,3));
  // sixth joints
  Jik[5]=atan2(-T36[2*4+1], T36[2*4+0]); // Jik(6)=atan2(-T36(3,2),T36(3,1));
  // rad to deg
  MatrixScale(Jik, 6, 1, 180.0/PI); // Jik=Jik/pi*180;
}

void ForwardK(float* Jfk, float* Xfk)
{
  // forward kinematics
  // input: Jfk - joints value for the calculation of the forward kinematics
  // output: Xfk - pos value for the calculation of the forward kinematics
  
  // Denavit-Hartenberg matrix
  float theTemp[6]={0.0, -90.0, 0.0, 0.0, 0.0, 0.0};
  float theta[6];
  MatrixAdd(theTemp, Jfk, 6, 1, theta); // theta=[Jfk(1); -90+Jfk(2); Jfk(3); Jfk(4); Jfk(5); Jfk(6)];
  float alfa[6]={-90.0, 0.0, -90.0, 90.0, -90.0, 0.0}; // alfa=[-90; 0; -90; 90; -90; 0];
  float r[6]={r1, r2, r3, 0.0, 0.0, 0.0}; // r=[47; 110; 26; 0; 0; 0];
  float d[6]={d1, 0.0, d3, d4, 0.0, d6}; // d=[133; 0; 7; 117.5; 0; 28];
  // from deg to rad
  MatrixScale(theta, 6, 1, PI/180.0); // theta=theta*pi/180;
  MatrixScale(alfa, 6, 1, PI/180.0); // alfa=alfa*pi/180;
  
  // work frame
  float Xwf[6]={0.0, 0.0, 0.0, 0.0, 0.0, 0.0}; // Xwf=[0; 0; 0; 0; 0; 0];
  
  // tool frame
  float Xtf[6]={0.0, 0.0, 0.0, 0.0, 0.0, 0.0}; // Xtf=[0; 0; 0; 0; 0; 0];
  
  // work frame transformation matrix
  float Twf[16];
  pos2tran(Xwf, Twf); // Twf=pos2tran(Xwf);
  
  // tool frame transformation matrix
  float Ttf[16];
  pos2tran(Xtf, Ttf); // Ttf=pos2tran(Xtf);
  
  // DH homogeneous transformation matrix
  float T01[16], T12[16], T23[16], T34[16], T45[16], T56[16];
  DH1line(theta[0], alfa[0], r[0], d[0], T01); // T01=DH1line(theta(1),alfa(1),r(1),d(1));
  DH1line(theta[1], alfa[1], r[1], d[1], T12); // T12=DH1line(theta(2),alfa(2),r(2),d(2));
  DH1line(theta[2], alfa[2], r[2], d[2], T23); // T23=DH1line(theta(3),alfa(3),r(3),d(3));
  DH1line(theta[3], alfa[3], r[3], d[3], T34); // T34=DH1line(theta(4),alfa(4),r(4),d(4));
  DH1line(theta[4], alfa[4], r[4], d[4], T45); // T45=DH1line(theta(5),alfa(5),r(5),d(5));
  DH1line(theta[5], alfa[5], r[5], d[5], T56); // T56=DH1line(theta(6),alfa(6),r(6),d(6));

  float Tw1[16], Tw2[16], Tw3[16], Tw4[16], Tw5[16], Tw6[16], Twt[16];
  MatrixMultiply(Twf, T01, 4, 4, 4, Tw1); // Tw1=Twf*T01;
  MatrixMultiply(Tw1, T12, 4, 4, 4, Tw2); // Tw2=Tw1*T12;
  MatrixMultiply(Tw2, T23, 4, 4, 4, Tw3); // Tw3=Tw2*T23;
  MatrixMultiply(Tw3, T34, 4, 4, 4, Tw4); // Tw4=Tw3*T34;
  MatrixMultiply(Tw4, T45, 4, 4, 4, Tw5); // Tw5=Tw4*T45;
  MatrixMultiply(Tw5, T56, 4, 4, 4, Tw6); // Tw6=Tw5*T56;
  MatrixMultiply(Tw6, Ttf, 4, 4, 4, Twt); // Twt=Tw6*Ttf;
  
  // calculate pos from transformation matrix
  tran2pos(Twt, Xfk); // Xfk=tran2pos(Twt);
  // Xfk(4:6)=Xfk(4:6)/pi*180;
  Xfk[3]=Xfk[3]/PI*180.0;
  Xfk[4]=Xfk[4]/PI*180.0;
  Xfk[5]=Xfk[5]/PI*180.0;
}

void invtran(float* Titi, float* Titf)
{
  // finding the inverse of the homogeneous transformation matrix
  // first row
  Titf[0*4 + 0] = Titi[0*4 + 0];
  Titf[0*4 + 1] = Titi[1*4 + 0];
  Titf[0*4 + 2] = Titi[2*4 + 0];
  Titf[0*4 + 3] = -Titi[0*4 + 0]*Titi[0*4 + 3]-Titi[1*4 + 0]*Titi[1*4 + 3]-Titi[2*4 + 0]*Titi[2*4 + 3];
  // second row
  Titf[1*4 + 0] = Titi[0*4 + 1];
  Titf[1*4 + 1] = Titi[1*4 + 1];
  Titf[1*4 + 2] = Titi[2*4 + 1];
  Titf[1*4 + 3] = -Titi[0*4 + 1]*Titi[0*4 + 3]-Titi[1*4 + 1]*Titi[1*4 + 3]-Titi[2*4 + 1]*Titi[2*4 + 3];
  // third row
  Titf[2*4 + 0] = Titi[0*4 + 2];
  Titf[2*4 + 1] = Titi[1*4 + 2];
  Titf[2*4 + 2] = Titi[2*4 + 2];
  Titf[2*4 + 3] = -Titi[0*4 + 2]*Titi[0*4 + 3]-Titi[1*4 + 2]*Titi[1*4 + 3]-Titi[2*4 + 2]*Titi[2*4 + 3];
  // forth row
  Titf[3*4 + 0] = 0.0;
  Titf[3*4 + 1] = 0.0;
  Titf[3*4 + 2] = 0.0;
  Titf[3*4 + 3] = 1.0;
}
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

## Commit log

2023-09-20 init push
    [Axis1Holder.SLDPRT, Axis1Holder.stl, Axis1MotorHolder.SLDPRT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]
2023-09-21 updates assembly
    [Axis1Holder.SLDPRT, Axis1MotorHolder.SLDPRT, Axis1MotorHolderOp.SLDPRT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]
2023-10-18 updates solidworks files
    [Axis2part1_2_print.SLDDRW, upper_assembly.SLDASM]
